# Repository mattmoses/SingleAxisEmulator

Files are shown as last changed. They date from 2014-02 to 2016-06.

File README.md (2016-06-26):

## Single Axis Stepper Motor Emulator

**_Overview_**          
This is a simple DC brushed motor controller with encoder feedback, step-direction interface, and optical home switch. It was originally built for a modular robotics application using low-power DC motors and very coarse (low resolution) encoders. This circuit may find application in CNC and 3D printing applications, but it is likely that certain modifications will need to be made (in software for example) to make use of higher resolution encoders. 

**_Principle of Operation_**   
The block diagram below illustrates the basic principle of operation. The microcontroller is a Microchip PIC 18F1320 and the motor driver is a LMD18200. Depending on the level of the Direction input, pulses on the Step line will increment or decrement an internal counter in the PIC. A separate counter tracks the actual position of the motor by decoding encoder pulses. An error signal is defined by the difference of the counter representing desired position and the one representing actual position. The LMD18200 receives a motor command that is simply proportional to the error. PID control is possible but not currently used. If the Step input is held high for longer than a certain threshold, the controller switches state to "homing mode" in which it runs the motor at constant speed until the optical home switch is activated. After the home switch is activated the controller returns to normal operation.

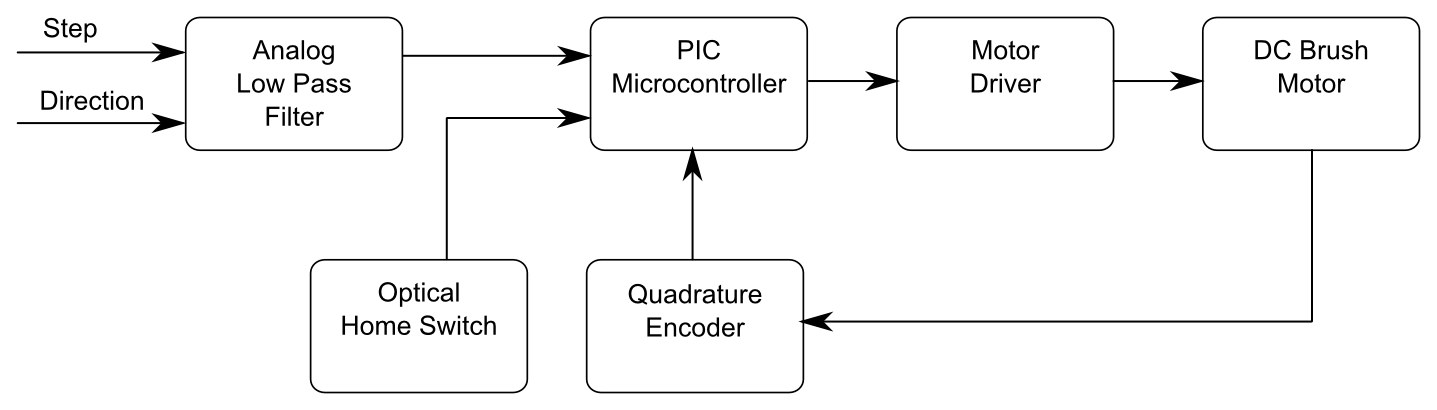
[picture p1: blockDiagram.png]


**_Downloads_**   
[Schematic](https://github.com/mattmoses/SingleAxisEmulator/blob/master/singleAxisMotor3.pdf)   
[Code](https://github.com/mattmoses/SingleAxisEmulator/tree/master/verticalMotor)     
[Gerber Files](https://github.com/mattmoses/SingleAxisEmulator/tree/master/gerbers)   
[Eagle PCB Files](https://github.com/mattmoses/SingleAxisEmulator/tree/master/eagleFiles)     
[Parts List](https://github.com/mattmoses/SingleAxisEmulator/blob/master/singleAxisMotor3_parts.txt)   

**_License_**   
This work is licensed under the [GNU General Public License](http://www.gnu.org/licenses/gpl.html).

**_How to Cite_**   
If you would like to reference this work in a publication, please refer to the [github url](https://github.com/mattmoses/SingleAxisEmulator) and cite this paper:

[An architecture for universal construction via modular robotic components](http://dx.doi.org/10.1016/j.robot.2013.08.005)    
*Robotics and Autonomous Systems*   
Matthew S. Moses, Hans Ma, Kevin C. Wolfe, Gregory S. Chirikjian (2013)

**_Credits_**   
This work was performed in [Gregory Chirikjian's](http://scholar.google.com/citations?user=qoIuyMoAAAAJ) [Robot & Protein Kinematics Lab](https://rpk.lcsr.jhu.edu/Publications) at Johns Hopkins University. The work was partially supported by the National Science Foundation under Grant No. IIS-0915542. Any opinions, findings, and conclusions or recommendations expressed in this material are those of the authors and do not necessarily reflect the views of the National Science Foundation.

Matt Moses created the schematic and ciruit board layout.    
Kevin Wolfe created the custom part library "modular_robot_parts.lbr".   
Kevin Wolfe authored the initial version of the control software.   
Matt Moses modified Kevin's original code. (Good parts belong to Kevin. Bad parts are Matt's fault.)   
John Swensen provided helpful advice.

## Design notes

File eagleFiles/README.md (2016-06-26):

These are schematic and PCB layout files created in Eagle PCB.

Eagle schematic: singleAxisMotor3.sch (Matt Moses)   
Eagle PCB layout: singleAxisMotor3.brd (Matt Moses)   
Custom part library 1: custom.lbr (Matt Moses)   
Custom part library 2: modular_robot_parts.lbr (Kevin Wolfe)   

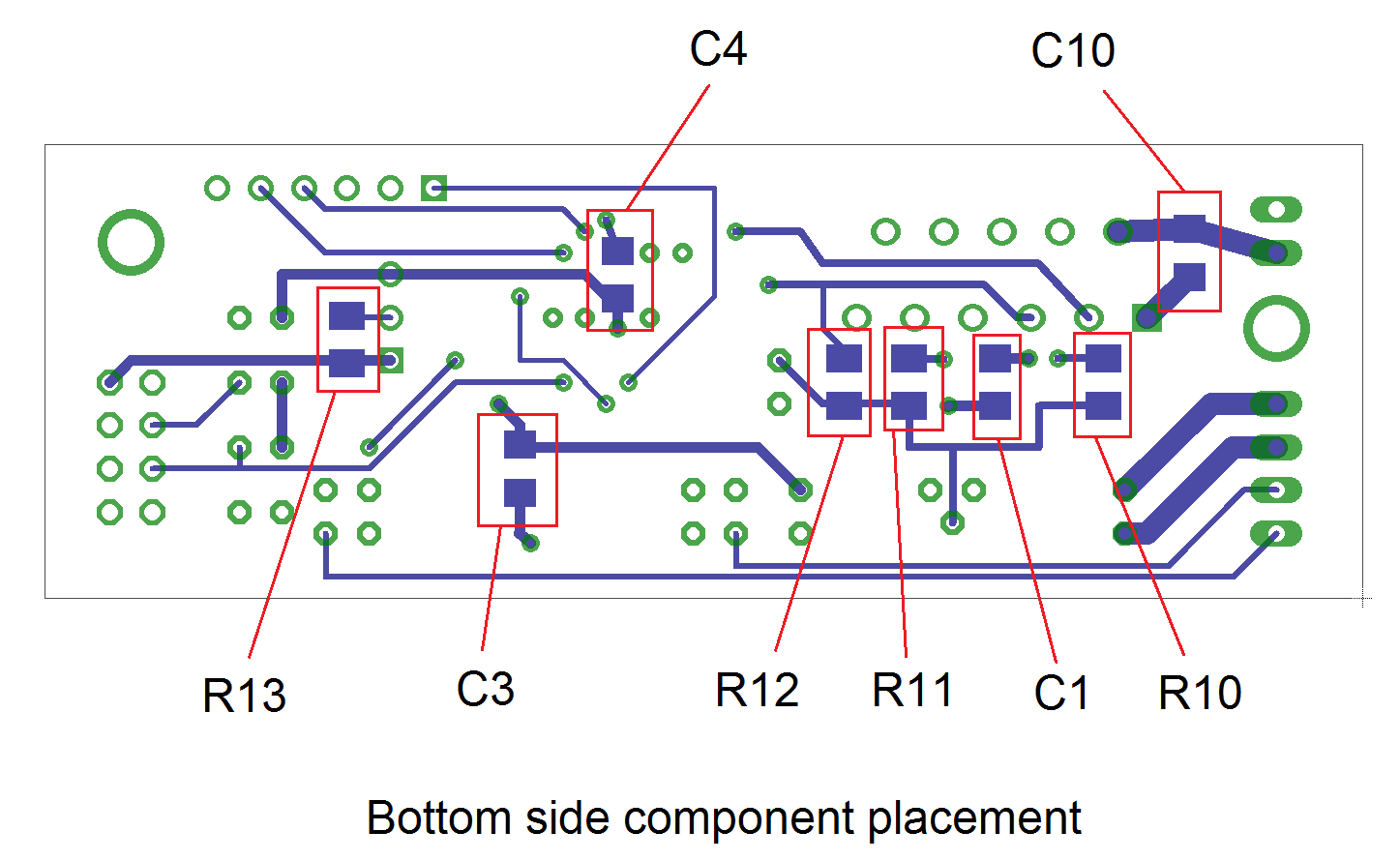
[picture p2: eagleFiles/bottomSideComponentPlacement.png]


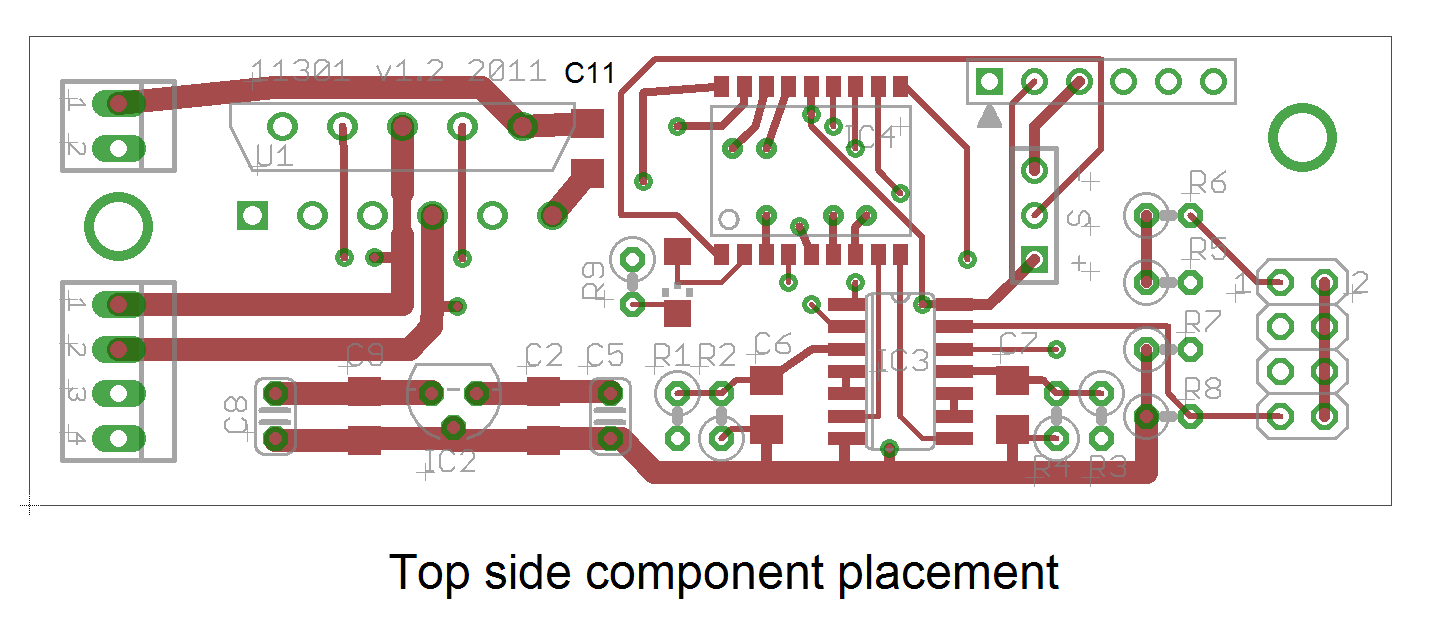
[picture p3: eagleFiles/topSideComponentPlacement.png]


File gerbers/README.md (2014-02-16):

These Gerber files were created in EAGLE PCB using the [Sparkfun CAM file](https://learn.sparkfun.com/tutorials/using-eagle-board-layout/generating-gerbers)   

Here are the layers:

| Layer | Ext. |
|:---:|:----:|
|Bottom Copper | GBL  |
|Bottom Soldermask | GBS  |
|Top Copper | GTL  |
|Top Silkscreen | GTO  |
|Top Soldermask | GTS  |
|Drill File | TXT  |

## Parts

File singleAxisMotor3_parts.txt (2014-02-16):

Partlist

Exported from singleAxisMotor3.sch at 2/16/2014 12:03:57 PM

EAGLE Version 6.5.0 Copyright (c) 1988-2013 CadSoft

Assembly variant: 

Part     Value                Device               Package        Library             Sheet

C1       0.1uF                C-USC1206            C1206          rcl                 1
C2       0.1uF                C-USC1206            C1206          rcl                 1
C3       0.1uF                C-USC1206            C1206          rcl                 1
C4       0.1uF                C-USC1206            C1206          rcl                 1
C5       10.0uF               C-US025-024X044      C025-024X044   rcl                 1
C6       10.0uF               C-USC1206            C1206          rcl                 1
C7       10.0uF               C-USC1206            C1206          rcl                 1
C8       1000uF               C-US025-024X044      C025-024X044   rcl                 1
C9       1.0uF                C-USC1206            C1206          rcl                 1
C10      10nF                 C-USC1206            C1206          rcl                 1
C11      10nF                 C-USC1206            C1206          rcl                 1
IC2      7805L                7805L                TO92           linear              1
IC3      40106D               40106D               SO14           40xx                1
IC4      PIC18F1320_18PIN_DIP PIC18F1320_18PIN_DIP SO-18W         modular_robot_parts 1
JP1      PIC_KIT_2_CONN       PIC_KIT_2_CONN       PIC_KIT_2_CONN modular_robot_parts 1
JP2                           PINHD-2X4            2X04           pinhead             1
LED1                          LEDCHIPLED_1206      CHIPLED_1206   led                 1
P1       3PIN                 3PIN                 3PIN           custom              1
R1       1k                   R-US_0207/2V         0207/2V        rcl                 1
R2       100k                 R-US_0207/2V         0207/2V        rcl                 1
R3       1k                   R-US_0207/2V         0207/2V        rcl                 1
R4       100k                 R-US_0207/2V         0207/2V        rcl                 1
R5       330                  R-US_0207/2V         0207/2V        rcl                 1
R6       330                  R-US_0207/2V         0207/2V        rcl                 1
R7       1k                   R-US_0207/2V         0207/2V        rcl                 1
R8       1k                   R-US_0207/2V         0207/2V        rcl                 1
R9       330                  R-US_0207/2V         0207/2V        rcl                 1
R10      1k                   R-US_M1206           M1206          rcl                 1
R11      2.7k                 R-US_M1206           M1206          rcl                 1
R12      10k                  R-US_M1206           M1206          rcl                 1
R13      10k                  R-US_M1206           M1206          rcl                 1
TP1      1PAD                 1PAD                 1PAD           custom              1
TP2      1PAD                 1PAD                 1PAD           custom              1
TP3      1PAD                 1PAD                 1PAD           custom              1
TP4      1PAD                 1PAD                 1PAD           custom              1
TP5      1PAD                 1PAD                 1PAD           custom              1
U1       LMD18200             LMD18200             TO-220-WIDE    custom              1
X1       22-23-2021           22-23-2021           22-23-2021     con-molex           1
X2       22-23-2041           22-23-2041           22-23-2041     con-molex           1

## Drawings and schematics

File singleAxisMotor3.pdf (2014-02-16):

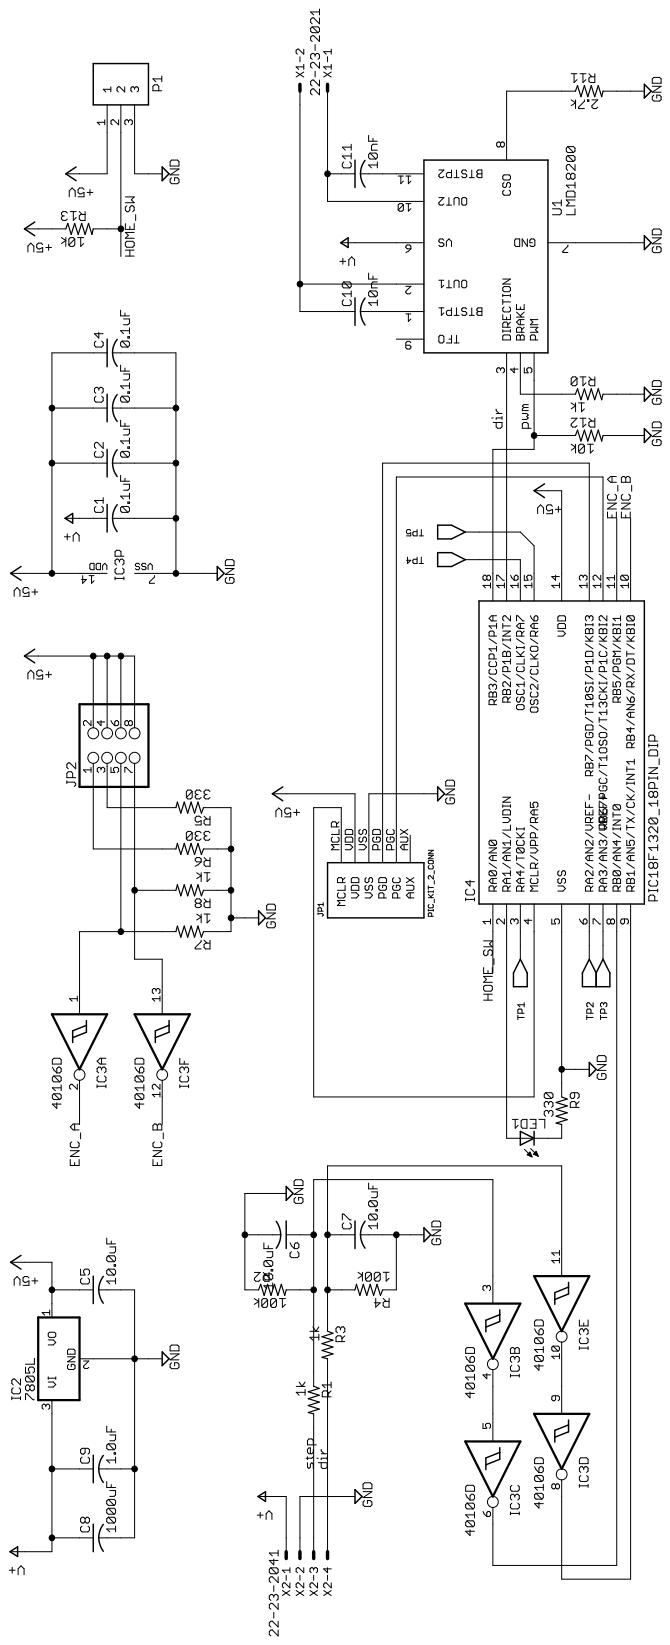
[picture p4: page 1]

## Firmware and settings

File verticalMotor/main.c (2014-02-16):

// Vertical motor driver code 
// Oringially made by Kevin Wolfe 2009-2011
// Modified by Matt Moses 2010-2011
// 

#include <p18f1320.h>
//#include <stdlib.h>
//#include <delays.h>
//#include <math.h>


#define counterToSpeedScalar 150
#define numCountsPerStep 1
#define maxSpeed 255
#define Kp 35.0
#define Kd 0.0
#define Ki 0.0
#define dt 0.01
#define speedStep 1
#define errorTol 1
#define tempADSpeed 255
#define stepHomeThreshold 500
#define upTorqueLimit 150
#define downTorqueLimit -120

#pragma config IESO = ON
#pragma config FSCM = ON
#pragma config OSC = INTIO2        
#pragma config PWRT = OFF
#pragma config BOR = OFF
#pragma config WDT = OFF
#pragma config MCLRE = OFF

/****** DISABLE LVP (LOW-VOLTAGE Programming) ******/
/* This allows RB5 to operate as an interuppt on change I/O pin */
#pragma config LVP = OFF
/***************************************************/

void low_isr (void);
void high_isr (void);
void set_motor_output (unsigned char desiredPWM, unsigned char desiredDirection);

#pragma code high_vector_section=0x8
void high_vector (void)
{
_asm GOTO high_isr _endasm
}
#pragma code

#pragma code low_vector_section=0x18
void low_vector (void)
{
_asm GOTO low_isr _endasm
}
#pragma code

volatile int stepHighCounter = 0;

volatile char stepPulses = 0;
//volatile int stepCounts;
volatile int currentCounter = 0;
//volatile unsigned char currentADvalue;
volatile unsigned char trigger = 0;
//volatile structPrevStates prevStates;
//volatile enum { DIR_CW = 0, DIR_CCW = 1 } direction;
volatile enum { LOW = 0, HIGH = 1} prevA = LOW;

// changeToggle is a varb used for debugging
volatile enum {LOW = 0, HIGH = 1} changeToggle;

#pragma interrupt high_isr
void high_isr(void)
{
	if ( INTCONbits.INT0IF ) //step pulse flag 
	{

		// reset stepTimerFoo
		stepHighCounter = 1;

		// do important stuff
		if ( PORTBbits.RB1 )    //Check direction pin
		{
			stepPulses++;
		}
		else
		{
			stepPulses--;
		}
	
		INTCONbits.INT0IF = 0; //reset step flag
	}

	if ( INTCONbits.RBIF ) //PORTB change interrupt
	{

//		// This is a little block for debugging - toggles A every time a change on PORTB
//	
//		if (changeToggle) {
//			changeToggle = 0;
//			PORTAbits.RA1 = 0;
//		}
//		else {
//			changeToggle = 1;
//			PORTAbits.RA1 = 1;
//		} 

		if ( PORTBbits.RB5^prevA )  	//CW Rotation
		{
			currentCounter++;
			//PORTAbits.RA1 = 0;
		}
		else						//CCW Rotation
		{
			currentCounter--;
			//PORTAbits.RA1 = 1;
//			if (changeToggle) {
//				changeToggle = 0;
//				PORTAbits.RA1 = 0;
//			}
//			else {
//				changeToggle = 1;
//				PORTAbits.RA1 = 1;
//			} 
		}


		prevA = PORTBbits.RB4;
		PORTAbits.RA1 = PORTBbits.RB5;

		INTCONbits.RBIF = 0; //resetQuadFlag
	}
}

#pragma interruptlow low_isr
void low_isr(void)  //timer interupt
{
	trigger = 1;
	INTCONbits.TMR0IF = 0; 			// reset TMR0 interrupt flag
}


void set_motor_output(unsigned char desiredPWM, unsigned char desiredDirection)
{
	if ( desiredDirection )
	{
		PORTBbits.RB2 = 0;
		CCPR1L = desiredPWM;  			// This is the register for the 8 MSB of the PWM pin RB3.
	}
	else
	{
		PORTBbits.RB2 = 1;
		CCPR1L = (desiredPWM );  	// This is the register for the 8 MSB of the PWM pin RB3.
	}
}

long abs(long i) 
{ 
	if (i < 0) 
		return -i; 
	else 
		return i; 
} 

char sgn(long i)
{
	if (i < 0)
		return -1;
	else if (i > 0)
		return 1;
	else
		return 0;
}


void main (void)
{
	long prevCounter = 0;
	unsigned char tempTrigger = 0; 
	char tempStepPulses = 0;
	long tempCurrentCounter = 0;
	
	unsigned char currentADvalue = tempADSpeed;
	long desiredCounter = 0;
	long error = 0;
	long prevError = 0;

	long velocity = 0;

	float integral = 0.0;
	float derivative = 0.0;

	long output = 0;

	char testState = 0;
	long testCounter = 0;



	char homeFlag = 0;
    enum { LOW = 0, HIGH = 1} homeDir = LOW;

	/*************** SETUP INTERRUPTS ******************/
	INTCONbits.GIEH = 0; 		// Temporarily disable global interrupts
	INTCONbits.GIEL = 0; 		// Temporarily disable peripheral interrupts
	INTCONbits.TMR0IE = 1; 		// Enable TMR0 Overflow interrupt
	INTCONbits.INT0IE = 1; 		// Enable external interrupt on INT0/RB0
	INTCONbits.RBIE = 1; 		// Enable Port B change interrupt

	//INTCON2bits.RBPU = 0; 		// Enable Port B pull-ups
	INTCON2bits.RBPU = 1; 		// Disable Port B pull-ups
	INTCON2bits.INTEDG0 = 1; 	// Interrupt on rising edge for INT0
	INTCON2bits.TMR0IP = 0; 	// Set TMR0 interrupt priority to Low
	INTCON2bits.RBIP = 1; 		// Set Port B change interrupt to High

	RCONbits.IPEN = 1;			// Enable priority levels on interrupts
	/****************************************************/




	/***************** SETUP TMR0 ***********************/
	//T0CONbits.TMR0ON = 0; 	// Temporarily disable TMR0 until the end of the setup;
	T0CONbits.T08BIT = 1; 	// Use an 8-bit timer (1). Use a 16-bit timer (0).
	T0CONbits.T0CS = 0; 	// Use internal clock cycles for the timer.
	T0CONbits.PSA = 0; 		// Use prescalar to adjust overflow rate (0). Do not use prescalar (1).
	
	/* Assign Prescalar */
	T0CONbits.T0PS2 = 0;
	T0CONbits.T0PS1 = 1;
	T0CONbits.T0PS0 = 1;

	/* This makes go slower */
	//T0CONbits.T0PS2 = 1;
	//T0CONbits.T0PS1 = 1;
	//T0CONbits.T0PS0 = 1;

	T0CONbits.TMR0ON = 1;
	/***************************************************/
	



	/************** SETUP I/O PINS *********************/
	TRISBbits.TRISB4 = 1;	// Encoder ChA input
	TRISBbits.TRISB5 = 1;	// Encoder ChB input
	TRISBbits.TRISB6 = 0;	// Set as output to avoid Port B interrupt on change 
	TRISBbits.TRISB7 = 0;	// Set as output to avoid Port B interrupt on change 

	TRISBbits.TRISB0 = 1;	// Step pulse input
	TRISBbits.TRISB1 = 1;	// Direction input

	//TRISAbits.TRISA4 = 0; 	// Possible motor output pin RA4

	TRISAbits.TRISA0 = 1;	// Set RA0 as input for SPEED pin (analog input for A/D)
	TRISAbits.TRISA1 = 0;	// Set RA1 as output for diagnostic LED

	//ADCON0bits.VCFG0 = 0;	// Set A/D to External Vref(+/-) using 1 and 1
	//ADCON0bits.VCFG1 = 0;	// Set A/D to Vss and Vdd references using 0 and 0
	/***************************************************/




	/**************** SETUP A/D ************************/
	/* Configure analog and digital pins */
	ADCON1bits.PCFG0 = 1; // Set AN0 port as digital input (Home switch)
	ADCON1bits.PCFG1 = 1; // RA1/AN1 diagnostic LED
	ADCON1bits.PCFG2 = 1; // Reserved - test pad on AN2
	ADCON1bits.PCFG3 = 1; // Reserved - test pad on AN3
	ADCON1bits.PCFG4 = 1; // Set AN4/RB0 as a digital pin (Step pulse input)
	ADCON1bits.PCFG5 = 1; // Set AN5/RB1 as a digital pin (Direction input)
	ADCON1bits.PCFG6 = 1; // Set AN6/RB4 as a digital pin (ChA input)
//
//	/* Select A/D input channel as AN0 */
//	ADCON0bits.CHS0 = 0;
//	ADCON0bits.CHS1 = 0;
//	ADCON0bits.CHS2 = 0;
//
//	/* Set A/D clock as Fosc/2 */
//	ADCON2bits.ADCS0 = 0;
//	ADCON2bits.ADCS1 = 0;
//	ADCON2bits.ADCS2 = 0;
//
//	ADCON2bits.ADFM = 0; // Left justify A/D conversion so only the 8 MSB are read later
//
//	/* Turn on A/D module */
//	ADCON0bits.ADON = 1;
	
	/* Turn off A/D module */
	ADCON0bits.ADON = 0;

	/***************************************************/




	/**************** SETUP PWM ************************/
	
	/* Configure PWM pins P1A and P1B as inputs. */
	TRISBbits.TRISB3 = 1;
	TRISBbits.TRISB2 = 1;

	/* Use PR2 to set the PWM period */
	PR2 = 0xFF;

	// Equation 15-1 PWM Period = [(PR2 + 1)] * 4 * TOSC * TMR2 Prescaler
	// or about 1 / 490Hz

	/* Set PWM Mode with P1A as a single modulated output */
	CCP1CONbits.CCP1M0 = 0;
	CCP1CONbits.CCP1M1 = 0;
	CCP1CONbits.CCP1M2 = 1;
	CCP1CONbits.CCP1M3 = 1;
	CCP1CONbits.P1M0 = 0;
	CCP1CONbits.P1M1 = 0;

	/* LSB of the PWM duty cycle */
	CCP1CONbits.DC1B1 = 0;
	CCP1CONbits.DC1B0 = 0;

	/* MSB of the PWM duty cycle */
	CCPR1L = 0x00;
	
	/* Configure TMR2 */
	PIR1bits.TMR2IF = 0;	// Clear interupt flag for TMR2 equal to PR2
	T2CONbits.T2CKPS1 = 1;  // Set prescaler to 16 to decrease PWM frequency
	T2CONbits.T2CKPS0 = 1;

	T2CONbits.TMR2ON = 1; // Turn on Timer2
	
	/* Wait for the TMR2IF flag go high before procedding */
	while (!(PIR1bits.TMR2IF))
	{
		int temp = 0;
	}	

	/* Set the PWM pins P1A and P1B as outputs. */
	TRISBbits.TRISB3 = 0;
	TRISBbits.TRISB2 = 0;

	ECCPASbits.ECCPASE = 0;
	/*****************************************************/

	/***************** SET OSC SPEED *********************/

    //OSCCONbits.IRCF0 = 1;
	//OSCCONbits.IRCF1 = 1;
	//OSCCONbits.IRCF2 = 1;

    OSCCONbits.IRCF0 = 1;
	OSCCONbits.IRCF1 = 1;
	OSCCONbits.IRCF2 = 1;

	/*****************************************************/
	


	// This line is part of the initial check sequence and is not
	// needed for normal operation:
	desiredCounter = 0;

	trigger = 0;
	stepPulses = 0;
	currentCounter = 0;
	


	set_motor_output( 0, 0 );


	/****************** ENABLE INTERRUPTS *****************/
	INTCONbits.GIEH = 1; 		// Enable global interrupts
	INTCONbits.GIEL = 1; 		// Enable peripheral innterupts
	/******************************************************/
	
	while (1)
	{

		INTCONbits.GIEH = 0;
			tempTrigger = trigger;
		INTCONbits.GIEH = 1;
		
		if ( tempTrigger )
		{	

			INTCONbits.GIEH = 0;
				trigger = 0;
				tempCurrentCounter = currentCounter;
				tempStepPulses = stepPulses;
				stepPulses = 0;

				// Check if step pin has been held HIGH.  If it has been held HIGH
				// long enough to indicate a HOME command, set home flag, otherwise
				// just increment stepHighCounter.  stepHighCounter gets reset in
				// in interrupt routine that reads step and direction lines.  
				if (stepHighCounter) {
					if (stepHighCounter > stepHomeThreshold) {
						homeFlag = 1;
						stepHighCounter = 0;
						homeDir = PORTBbits.RB1; //set home direction to direction input pin
					}
					else {
						if (PORTBbits.RB0) {
							stepHighCounter++;
						}
					}
				}
				//stepTimerFoo++;
				//tempStepTimerFoo = stepTimerFoo;
			INTCONbits.GIEH = 1;
	


	
			// if tempStepTimerFoo > something 
			//    then set homeFlag, set homeDir

			// if homeflag
				// if homeswitch
				//		turn off homing
				//	else
				//		set motor go to home in homeDir direction
				//	end
			//else
			//	do normal motor control
			//end
				
		




/*
			INTCONbits.GIEH = 0;
				trigger = 0;
			INTCONbits.GIEH = 1;

			

			//if (PORTAbits.RA1)
			//	PORTAbits.RA1 = 0;
			//else
			//	PORTAbits.RA1 = 1;

			INTCONbits.GIEH = 0;
				tempCurrentCounter = currentCounter;
				tempStepPulses = stepPulses;
				stepPulses = 0;
			INTCONbits.GIEH = 1; */

		//	velocity = (tempCurrentCounter - prevCounter)*counterToSpeedScalar;
		//	prevCounter = tempCurrentCounter;

				
			// Uncomment this for normal operation
			desiredCounter = desiredCounter + (tempStepPulses*numCountsPerStep);
			


			if (homeFlag) // If we are in homing mode
			{
				if (PORTAbits.RA0) // if homeswitch is ON
				{
					// We're home!
					set_motor_output(0,0);
					homeFlag = 0;
					desiredCounter = 0;
					
					// turn off interrupts to clear sensitive variables
					INTCONbits.GIEH = 0;
						currentCounter = 0;
					INTCONbits.GIEH = 1;
				}
				else // if homeswitch is OFF - we are still going home
				{	 
					if (homeDir) // going up
					{
						set_motor_output(abs(upTorqueLimit),1);
					}
					else // going down
					{
						set_motor_output(abs(downTorqueLimit), 0);
					}
				}
			}
			else
			{
				error = desiredCounter - tempCurrentCounter;
				output =  Kp * error;

				////////////// Set motor output //////////////////////////////
				//
				// The variable "output" controls voltage to motor. Examples:
				//
				// this makes the motor go up:
				// set_motor_output(30,1);
            	//
				// this makes the motor go down:
				// set_motor_output(30,0);
				//
				if (output <= 0)
				{
					if (output < downTorqueLimit)
					{
						output = downTorqueLimit;
					}
					set_motor_output(abs(output),0);
				}
				else
				{
					if (output > upTorqueLimit)
					{
						output = upTorqueLimit;
					}
					set_motor_output(abs(output),1);
				}
			}
		}
	}
}

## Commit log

2014-02-16 added schematic and gerbers
    [singleAxisMotor3.GBL, singleAxisMotor3.GBS, singleAxisMotor3.GTL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]
2014-02-16 added initial round of eagle files
    [singleAxisMotor3.brd, singleAxisMotor3.sch]
